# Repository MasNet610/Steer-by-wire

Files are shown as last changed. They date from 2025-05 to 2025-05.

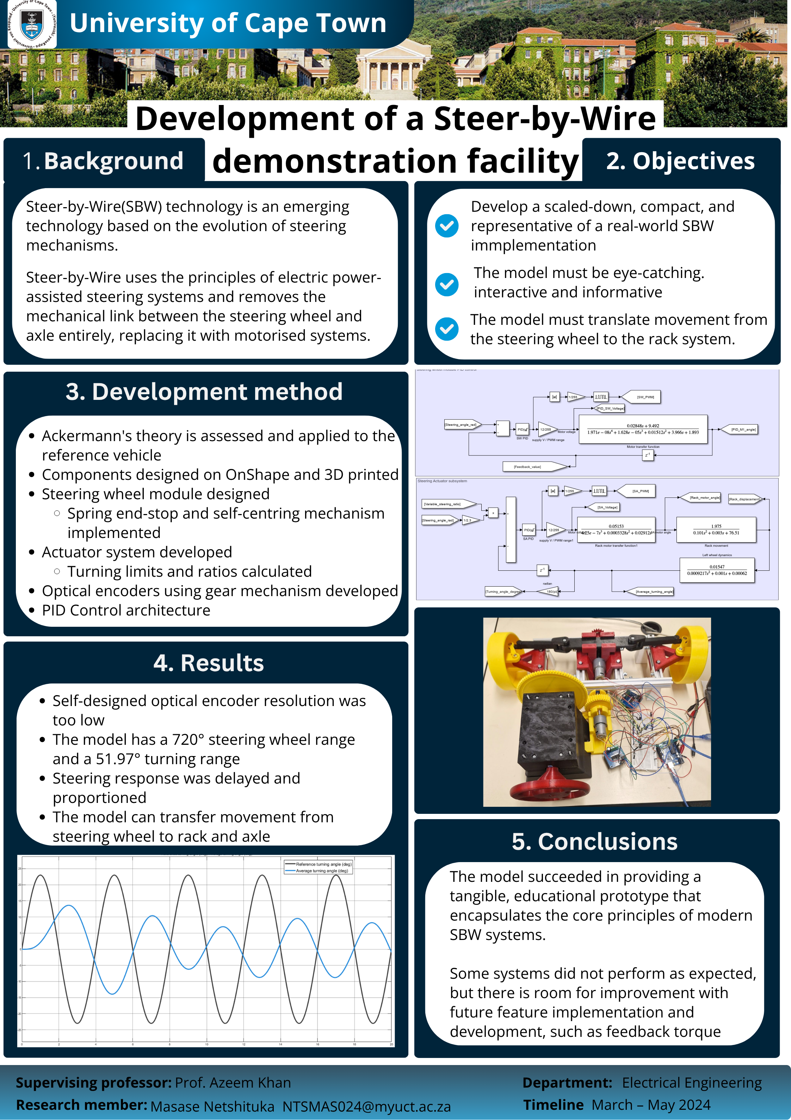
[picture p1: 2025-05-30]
Documentation/V4.png

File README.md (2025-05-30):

# Steer-by-wire

This project presents the development of a compact, pseudo-realistic Steer-by-Wire (SBW) demonstration facility
aimed at showcasing the core concepts and operational principles behind modern vehicle steering systems. The
model replicates the structure and function of commercial SBW implementations, emphasizing modular design,
electronic control integration, and mechanical realism within a scale-appropriate prototype. Core subsystems
include a steering input module, an electronic control unit (ECU), and a steering actuation module, all designed
with real-time signal interchange and actuation dynamics. The model prioritizes educational value, system
scalability, and ease of future enhancement. Comprehensive testing and literature integration guide the design
process, balancing mechanical accuracy with cost, space, and feasibility constraints. This facility serves as both
a learning platform and a foundation for further research into steer-by-wire technologies.

NOTES:
Changes that need to be made post project completion:
- Steering Wheel Motor returned is a 65rpm motor, however, the model is designed around a 270rpm motor (as noted in the report) that was provided by the student.
- MATLAB and circuit layout are designed for Arduino UNO. However, it does not have enough memory to operate adequately
- Rack and pinion sizes should be recalculated

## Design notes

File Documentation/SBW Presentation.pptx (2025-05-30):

## Development of a Steer-by-Wire demonstration facility

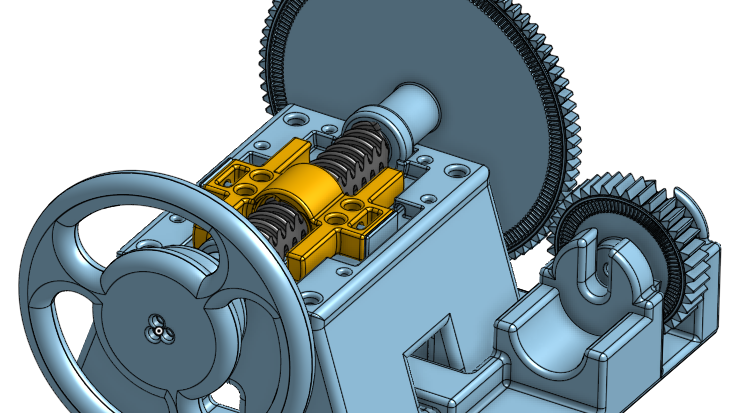
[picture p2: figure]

Researcher: Masase Netshituka

Supervisor: Prof. Azeem Khan

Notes: Less text

## Project background

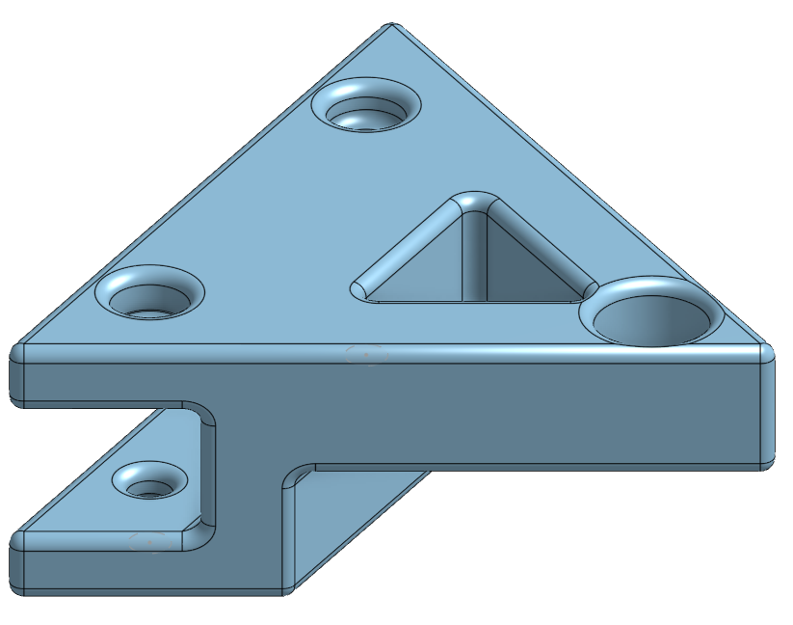
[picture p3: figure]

Steer-by-Wire(SBW) is an emerging technology based on the evolution of steering mechanisms.
The tech is based on EPAS systems.
SBW removes the mechanical link between the steering wheel and axle entirely.
Purpose of this project is to develop an interactive and educational model for demonstration.

## Research

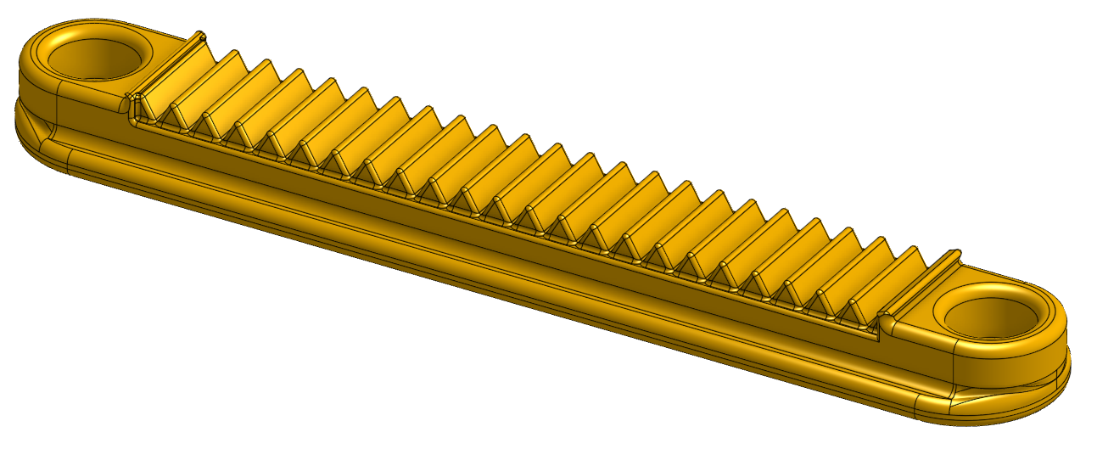
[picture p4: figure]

Current systems

- Common steering systems:
  - Synchronous steering
  - Rack-and-Pinion
- Different Power Assisted Steering (PAS) systems:
  - Hydraulic power steering (HPAS)
  - Electro-hydraulic power steering (EHPAS)
  - Electric power steering (EPAS)

Steer-by-Wire

- Advantages:
  - Highly flexible design
  - Highly efficient
  - Easy to integrate
  - Increased crash safety
  - Highly tailored experience
- Disadvantages:
  - Highly complex
  - Reliability concerns
  - High initial implementation cost

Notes: Advanced driver assistance system

## Model development

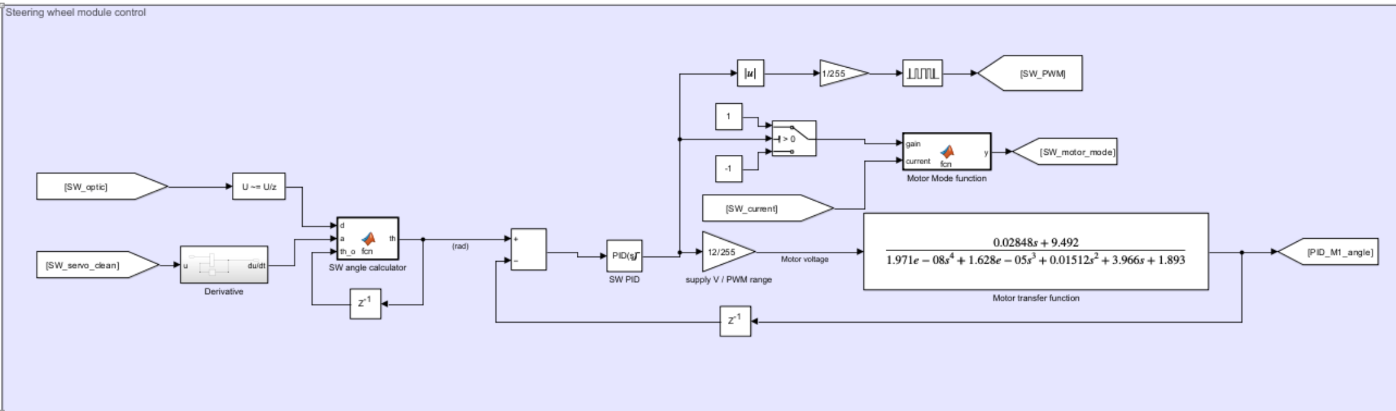
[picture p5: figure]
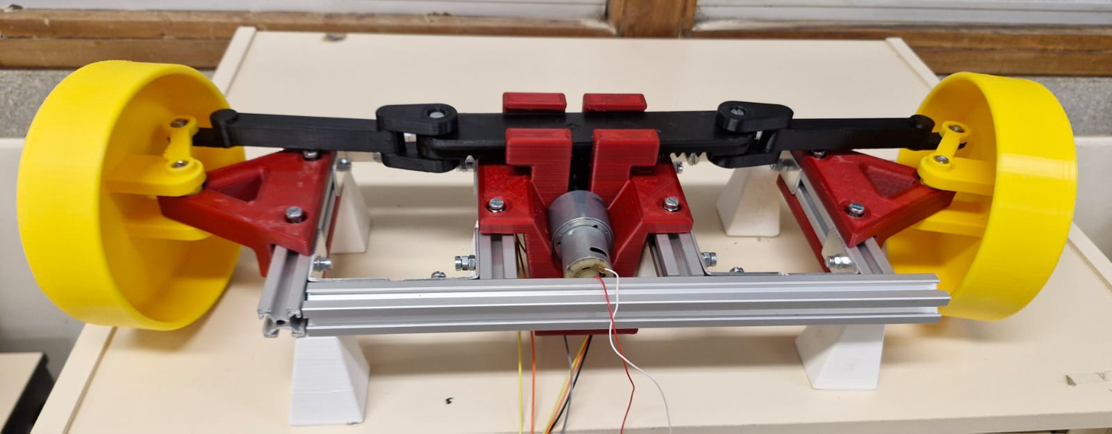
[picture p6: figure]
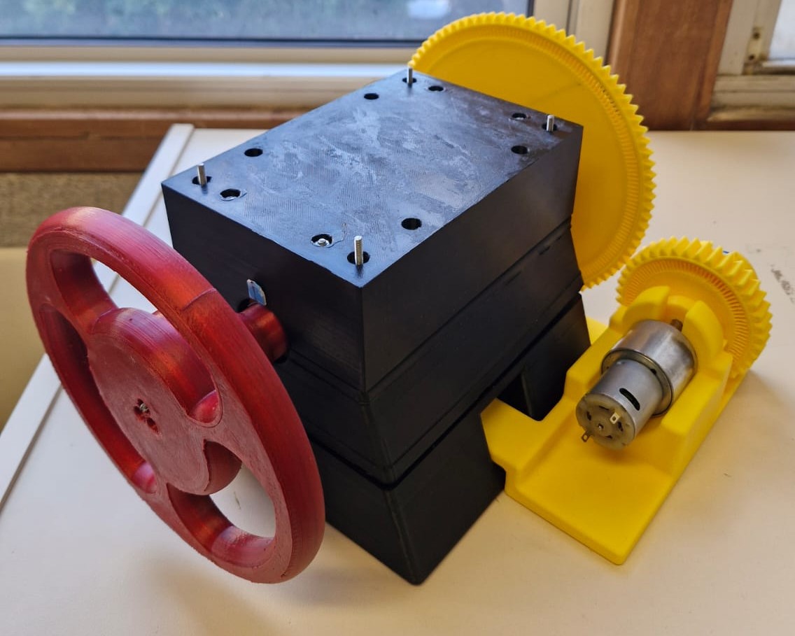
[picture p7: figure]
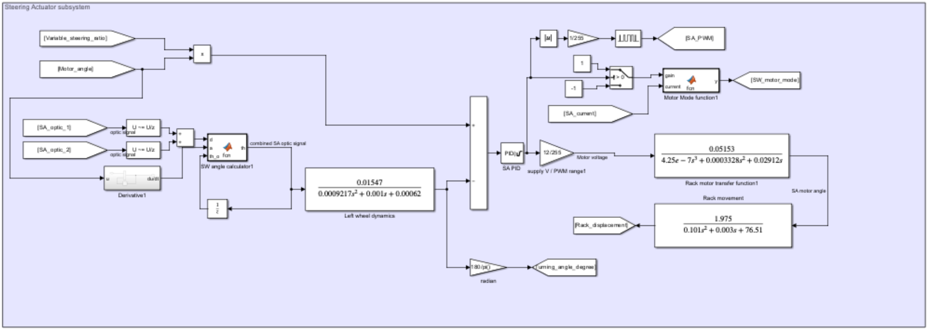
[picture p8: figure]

## Steering Wheel module design

Design objectives:
720° Steering range
Durable design
Recentring system
± 1° steering angle resolution
120 rpm wheel rotation

Design components:
- End-stop housing system
- Self-centring mechanism
- Custom rotary encoder
  - potentiometer
- 2.3 : 1 gearing ratio with 12V 270rpm motor

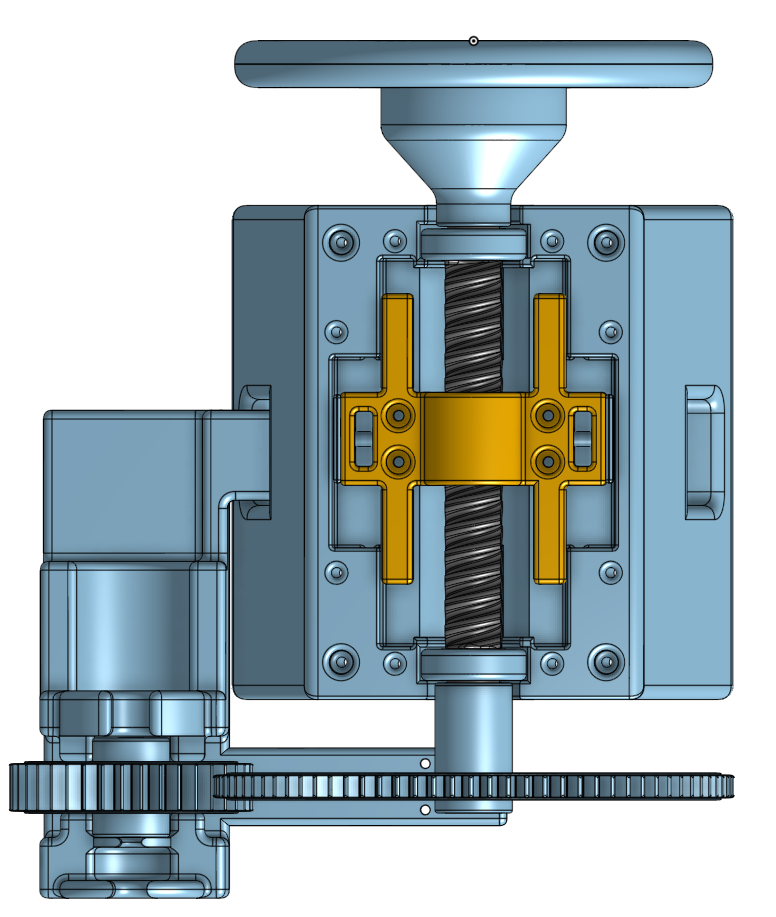
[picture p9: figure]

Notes: Mention that feedback torque was not implemented
Add SW as actual image, not background

## Steering Actuator module design

Design components:

- Rack-and-pinion base design
- 60rpm motor
- Grey-code rotation direction
- 1:3 scale of Suzuki Fronx

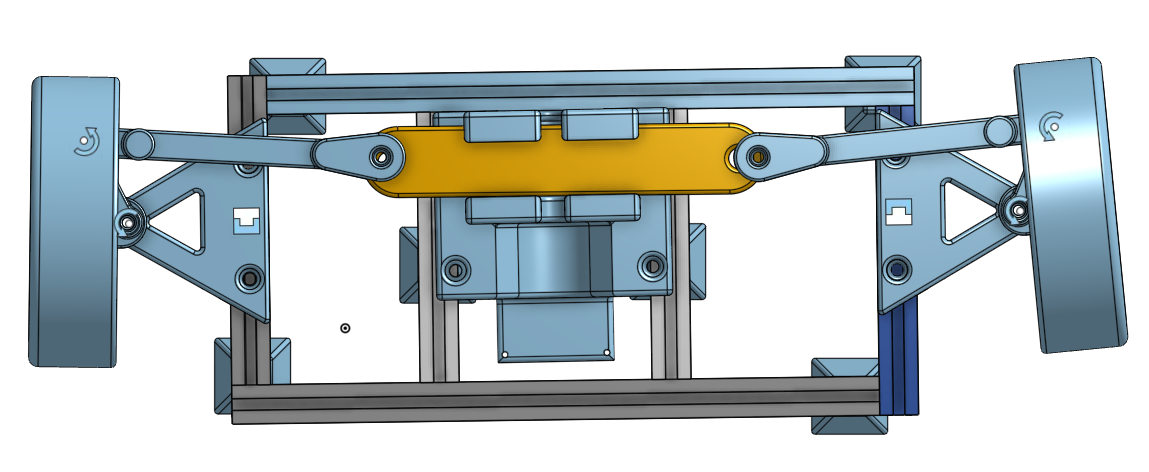
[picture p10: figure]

Design objectives:

46,42° ± 4,6° Turning range
End-to-end turn in 1s
Ackermann theory fulfilment
± 1° steering angle resolution
Small scale

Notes: Bring image to the front

## ECU and Control

Design objectives:
Smooth steering response
< 2s delay in response
<5% transient state overshoot

Hardware:
- Arduino Uno microcontroller
- 4 Quadrant drivers
- Use of MATLAB/SMULINK
- PID based control

Software:
- EOMs derived and converted into transfer functions
- PID based control methodology
- 2 loop system:
  - Steering wheel module
  - Steering Actuator module

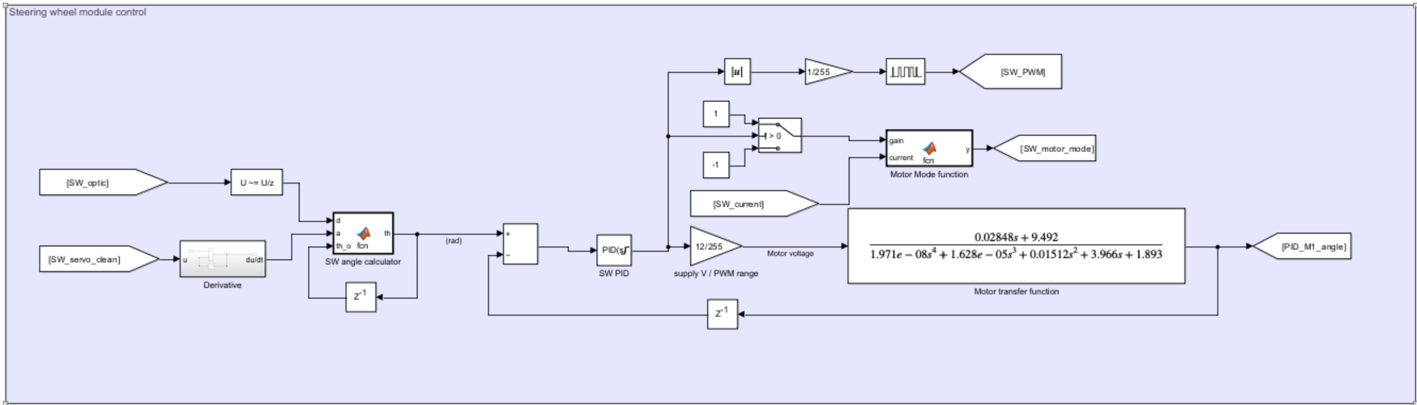
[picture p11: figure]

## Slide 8

## Results

- System tracked with a damped step with 5,2s, sinusoid in1,4s delay
- Steering range of 52° (11,2%)
- Ackermann criteria upheld
- Custom encoder system functioned, but faced precision issues
- Full-range steering in 1s achieved.
- Recentering system faced challenges
  - Stronger springs
  - Refined steering shaft thread angle
- 475 mm x 545 mm overall dimensions

Step response

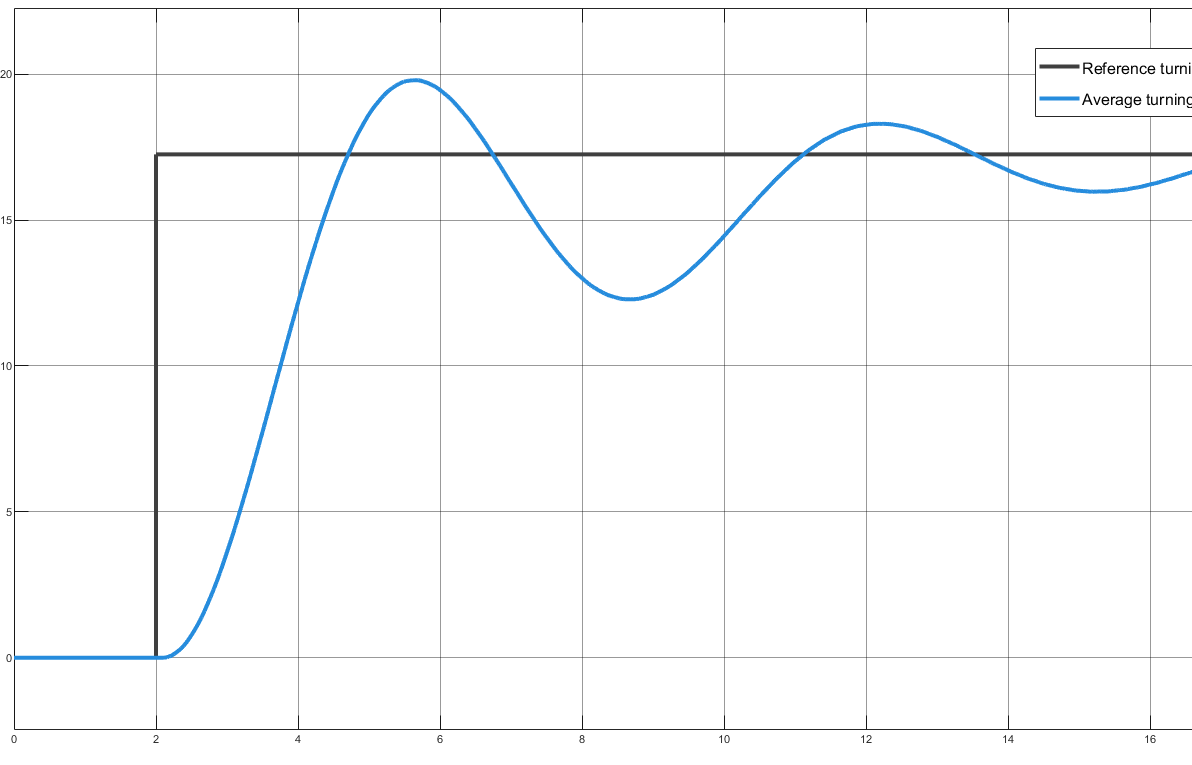
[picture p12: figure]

0,25Hz sinusoid response

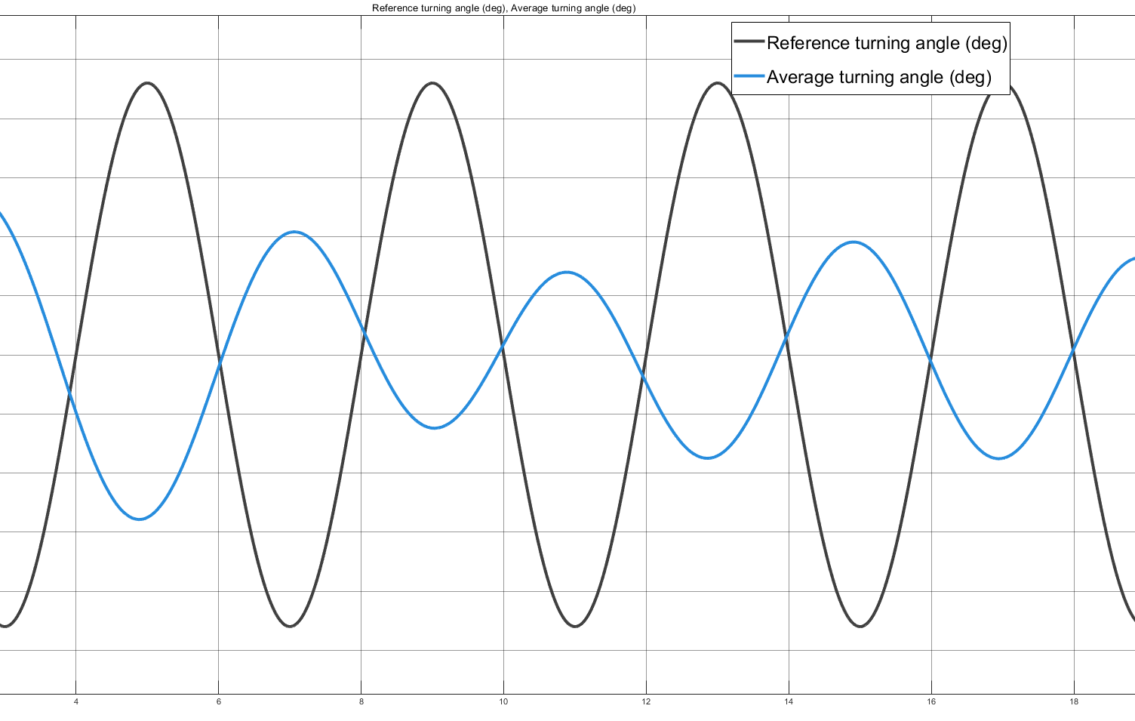
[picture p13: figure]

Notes: Put heading for graphs

## Recommendations

Conclusion

- Design is a functional display and representation of the SBW system, despite the challenges faced.
- Core principles of SBW and rack-and-pinion steering are evident with wireless steering communication achieved.

Larger spring constant
Improved shaft thread design
Recalculation of rack and tie-rods
Implementation of Feedback torque
Microcontroller with more memory

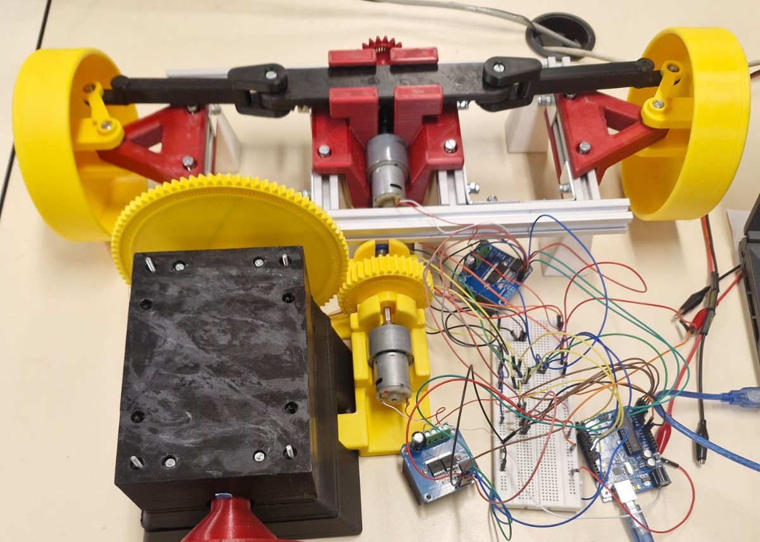
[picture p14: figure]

## THANK YOU

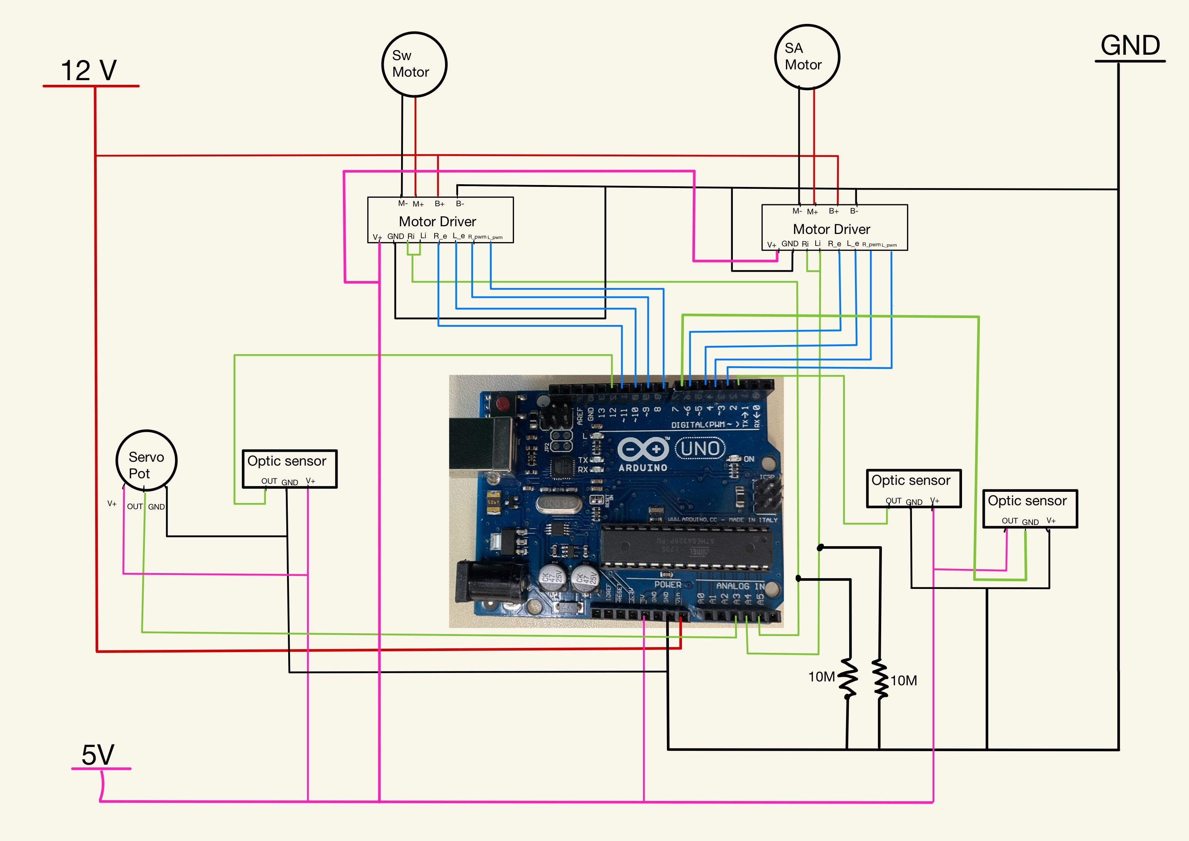
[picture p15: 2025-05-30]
Circuit diagram/ECU circuit.jpg

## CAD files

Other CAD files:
3D component files/Steering Actuator/Tie rod v2.stl
3D component files/Steering Wheel/Steering motor gear.stl
3D component files/Steering Actuator/Rack.stl
3D component files/Steering Wheel/Steering wheel box - Base bottom.stl
3D component files/Steering Actuator/Actuator motor mount.stl
3D component files/Steering Wheel/Sliding spacers.stl
3D component files/Steering Actuator/Wheel hub - Right wheel-hub.stl
3D component files/Steering Wheel/Steering wheel gear.stl
3D component files/Steering Actuator/Support leg.stl
3D component files/Steering Wheel/Steering wheel box - Shaft slider.stl
3D component files/Steering Actuator/Pinion Gear.stl
3D component files/Steering Wheel/Steering motor mount.stl
3D component files/Steering Actuator/Wheel hub - Left wheel-hub.stl
3D component files/Steering Actuator/Wheel support.stl
3D component files/Steering Wheel/Shaft bushing.stl
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

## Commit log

2025-05-30 Clean initial commit with STL files
    [Actuator motor mount.stl, Pinion Gear.stl, Rack.stl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]
2025-05-30 Added circuit diagram directly and put notes in the ReadME
